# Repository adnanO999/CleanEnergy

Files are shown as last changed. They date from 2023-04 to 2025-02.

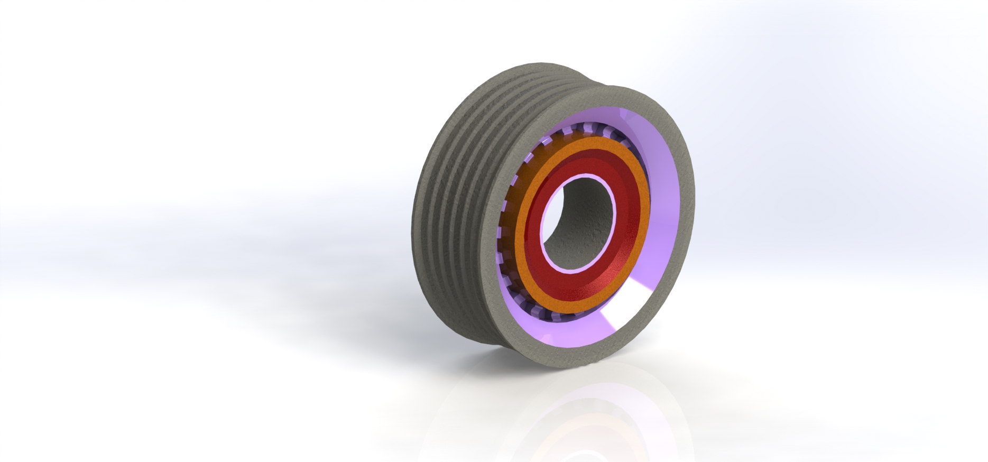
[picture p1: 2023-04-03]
SolarPanelCleaner/cad_parts/RoverCAD/pulley/PULLEY.JPG

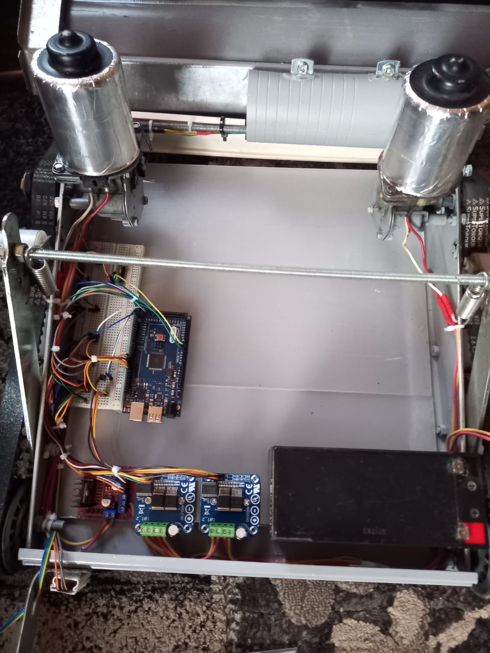
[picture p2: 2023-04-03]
SolarPanelCleaner/robot_pictures/wiring2 (2).jpeg

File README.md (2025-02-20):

# CleanEnergy
onsolarpanel

As it is obvious, the project is designed to clean solar panels. It might be an easy task however from simple observations, several problems might arise such as difficulties in covering the entire area, electrocution. Therefore I decided to build this project for the Mechatronics System design I. However I took one step further and used computer vision to detect the area of cleaning instead of relying only on sensors.

In this article I will be focusing on the implementation of each part and mainly the mechanical design wich was the core of the project and I was responsible of carrying out the design and implementation along with other tasks taht will be mentioned in what follows.

The project can be devided in several parts:
* Research 
* Mechanical design 
* assembling and wiring hardware 
* Code 
   * S shape path1 and path2 
   * Bluetooth communication/app 
   * MPU 6050 
* Report/presentaion
* Additional Improvements outside the course scope (personal work)

Each part will be expalined along

# Research and Motivation
## Dust and Efficiency Reduction


Solar energy is the most abundant of all energy resources and can be easily employed through the installation of solar panels constructed of photovoltaic cells (PV) that converts the sun radiation to electricity by a process of photon absorption and electrons excitation. 

However solar panels could experience efficiency reduction due to accumulated dust or unclean panels blocking solar radiation from interacting with PV cells. This is a major issue since the light obstruction materials (accumulation of dirt or particles like dust, sand, and moss) pose as external resistances that reduce solar photovoltaic performance. It was found that the external resistance could reduce the photovoltaic performance by up to 85% and the value of short circuit current, power decrease with respect the amount of dust on the solar panel.

## Modular Design and Angle Obstacle


we can notice that the first obstacle is the issue related to the angle. If we need to build a robot, we need to overcome slope slippage. This is a main challenge since our target is to build modular cleaning mechanism capable of covering different solar panels installation rather than static mechanism such as conventional wipers available for large firms

# Mechanical Design: Caterpillar Model

The previous issue of slopes cannot be resolved using a standard wheel-based robot since these types of robots have small wheels providing reduced contact area with the surface. Any plastic wheel will fail to provide the necessary grip to overcome slopes.
For this purpose I started my research and opted for caterpillar design. However the available robots in the market were very small or made of plastic which will not help.
For this reason I started several design iterations listed below with a brief description:

## Fisrt Design: Use of Car Seat and Customized Belts

As we can see the chassis is made of a car seat which was our initial starting point. We wanted to use the back of the seat as our cleaner since it had the ability to move up and down. Moreover we did not have appropriate belts thus we needed to cut one long belt and connect it. We discovered that the belts were not strongly bonded which will create slippage problems and malfunctioning when moving from one panel to the other

## Second Design: Customized Chassis Design and Use of car Window Motor

As we can notice this time, we designed a new compact chassis that include polyamide wheels that will help us moving from one panel to the other easily. Moreover, we can notice that we added a gear and motors to make the caterpillar move. However, the gears were customized to fit the belt teeth which led to slippage once some teeth were jumped over. To solve this problem, we needed to maintain good contact with our gear. This will be done using pulleys that compress the belt to the gear. 

## Third Design: New Belts and Use of Wiper Motor 

In this design we can see an enhancement of the previous design by adding fixed pulley to press the belt toward the gear. As such we avoid the case of belt’s teeth jumping more than one at a time. However, the problem is in the rigidity of the fixed pulley. When stress is coming from the bottom part, the belt will be in excessive tension around the gear which affects motion. To avoid this problem, we must use modular pulley to compress the belt toward the gear

## Fourth Design: Final Chassis Design 
### Tensioner Design: Unique Approach 


To move from fixed to modular pulley we were inspired by the car mechanism “tensioner.” We tried to implement a similar behavior by allowing pulley to move by spring mean. This design allows us to reduce tension on the gear when moving from panel to another and in case the panels are not aligned at the same height this will insure a perfect transition. 

 By following the distinctive design procedure, we successfully designed a differential rover capable of defeating and climbing slops. Our final chassis model is in the adjacent picture. As we can see the robot is standing on the panels without any problem.  
The effort put in the mechanical design is a considerable effort since it is not a conventional design available in the market. The rover is a customized and assembled part by part from different components that include customized belts, car pulleys used as wheels, polyamide wheels, and copper tubes fixing the wheels to the chassis, springs to support the moving pulley. We can say that as first step which is the base of the project is achieved by producing a successful model able to climb slopes. 

## Cleaning Mechanism: Gears and Chains to Convert and Translate Motion

The cleaning mechanism can be considered as our second challenge. The main difficulty consists in ensuring a brush able to clean the distance traveled by the robot. This can be done using two separate disks rotating each having a diameter equal to half the width of the robot. This is technically realizable however it implies the need of two motors each for one brush or the use of gear assembly like the differential gear where two brushes will be rotated by one motor. The second solution is to use one a single brush able to cover the width of the robot and a motor attached at one end. The problem faced in this approach was the motor installation which was solved by adding chain and gears between the motor and brush.

# Motor Selection
We applied the concepts learned throught the course, and detailed calculation was carried out to find a suitable motor. Ater all calculation we selected wiper motors.

# Wiring and Connections
All connections and wires were organized to have the best wiring schematic. Clean wiring to avoid connections issues. This is shown below:



# Algorithm
For the algorithm we used simple approach that relies on IR sensor to detect the presence of panel under the robot and using S shape algorithm we navigated along panels. Two issues arised:
## Chassis Drift: Motor Synchronization
Since we did not have encoders on our mototr we could not use encoder feedback to run the two motors at same speed therefore we relied on PWM signals and made the slowest motor's speed to be the mazimum speed. However a slight deviation remained, this problem will be solved as explained below:

## Which Direction to Rotate: Left or Right?
Since our design is modular and the user can put the robot on any corner, we need to be able to know our orientation. This problem is solved using MPU6050 where we read the angle to know if we are tilted left or right. To benefit more from the MPU6050 we used the acceleration and derived velocity combining with tilt angle to allow the robot to adjust its pose when deviating 

To test the accelerometer data, we coolected hundred of samples serialy through a python code which converts the reading to a csv file that can be ploted in matlab. We used matlab to analyze and process the data and the results obtained are shown below (we should mention that MPU6050 readings are noisy and drift with time therefore filters were used):




# Bluetooth Application
To give the user the ability to better ontrol the rover in case of any failure, We created a bluettoth application that helps navigating the robot. The application was built using MIT app and the hardware used was HC-05 bluetooth module:


# Further Work
## Computer Vision
This feature was under developement that allows the user to take a picture and send it to the rover allowing it to visualize and calculate the cleaning surface.
(the testing was done only on the PC since I did not establish a wireless connection between the rover and PC)
WhatsApp Image 2023-05-28 at 17 26 29

## Solidworks Model
I tried to design a solidworks model for further design enhancement



## Tracking the Rover
To obtain a closer look on how the robot is moving, I previously created a program that ensures communication between arduino, python and unity game engine.
The process works as follows: we need to add encoders to be able to get the better measurements for the displacement. Displacement and values accumulated MPU6050 can be combined and sent from aduino to python serialy (later we can use raspberrypi to eliminate the use of cable). The data collected in sent from python to unity and through a C# script I created a TCP or UDP connection based onpreference and the accuracy of data send and communication type. I followed an existing model to create this communication with a small modification in order to recieve the data in the correct format and shape.

# Summary
Solar panel cleaning rover This project aims to clean solar panels in more efficient and safe way. The design process followed several iterations and endedup using caterpillar model. The rover is designed to handle differnt slopes varying from 0 to 30 degree. A modular tensioner is mounted on both sides to enable smooth transition from on panel to the other and accomodate with height difference when moving across the panels. The Robot weight approximately 10 Kg however this weight can be reduced by removing the water tank and battery from the rover and mount them externally. S shape algorithm was used based on accelerometer and gyroscope data (pitch roll yaw angles) and projected on the panels surface. the microncontroller used was arduino mega thus processing was limited therefore I used serial communication to build python program to handle computer vision. Matlab and python codes were built using existing examples however with more modification to match our goal. These codes were used to collect data from accelerometer/gyroscope transform them to csv file and plot them to analyze the movement of the robot.

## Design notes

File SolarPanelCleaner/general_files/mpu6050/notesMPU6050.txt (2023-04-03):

1)IMU with 6 DOF. device contains gyroscope and accelerometer used to measure
inertia position rotation...

2)acceleration vs inertial force acting on the accelerometer (work in opposite direction)

3)guroscope used to measure angle orientation on three different levels(pitch rol yaw)
mems technology used in mpu6050. when an axis is rotated a voltage is produced.Voltage is sampled 
with 16 bits ADC inside the MPU6050

4)temperature sensor is implemented on the MPU6050 and DMP(digital motion process)
used to corrolate data from accelerometer and gyroscope

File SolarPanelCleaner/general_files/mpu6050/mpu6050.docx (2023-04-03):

1)IMU with 6 DOF (ability to move in three dimensions). device contains gyroscope and accelerometer used to measure

inertia position rotation...

2)acceleration vs inertial force acting on the accelerometer (work in opposite direction)

3)guroscope used to measure angle orientation on three different levels(pitch roll yaw)

mems technology used in mpu6050. when an axis is rotated a voltage is produced.Voltage is sampled

with 16 bits ADC inside the MPU6050

4)temperature sensor is implemented on the MPU6050 and DMP(digital motion process)

used to corrolate data from accelerometer and gyroscope

pin configuration

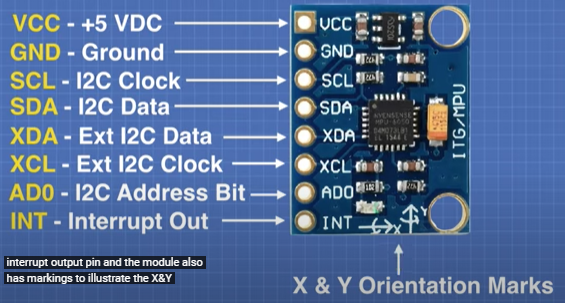
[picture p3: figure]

Info: https://www.dofbot.com/post/angle-measure-using-mpu-6050-3-axis-accelerometer-and-gyroscope-sensor

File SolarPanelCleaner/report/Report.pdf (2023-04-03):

# LEBANESE AMERICAN UNIVERSITY

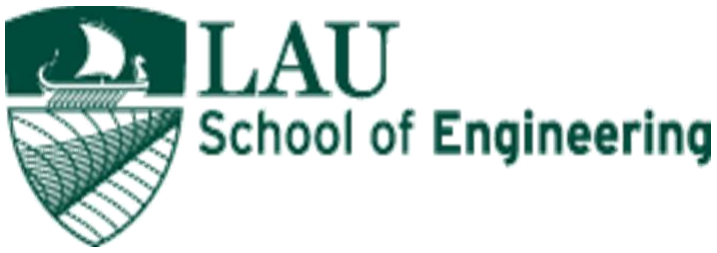
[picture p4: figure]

# Mechatronics System Design I Final Project

## Instructor: Dr Bilal Komati

## Dustbuddy: The Autonomous Solar Panel Cleaner

Table of Contents

Table of Figures
Figure 1 I-V characteristic and external resistance effects |
6
Figure 2 clean versus dusty solar panels |
7
Figure 5 first design (car seat chassis) |
10
Figure 9 Final chassis design defeating slopes (https://d.docs.live.net/2f20193610db98f5/Desktop/MCE_report%20edit.docx#_Toc122398008) . (https://d.docs.live.net/2f20193610db98f5/Desktop/MCE_report%20edit.docx#_Toc122398008) |
12 (https://d.docs.live.net/2f20193610db98f5/Desktop/MCE_report%20edit.docx#_Toc122398008)
Figure 10 Cleaning Mechanism (https://d.docs.live.net/2f20193610db98f5/Desktop/MCE_report%20edit.docx#_Toc122398009) . (https://d.docs.live.net/2f20193610db98f5/Desktop/MCE_report%20edit.docx#_Toc122398009) |
12 (https://d.docs.live.net/2f20193610db98f5/Desktop/MCE_report%20edit.docx#_Toc122398009)
Figure 11 Arduino Mega ADK |
13
Figure 13:BTS7960 (https://d.docs.live.net/2f20193610db98f5/Desktop/MCE_report%20edit.docx#_Toc122398012) . (https://d.docs.live.net/2f20193610db98f5/Desktop/MCE_report%20edit.docx#_Toc122398012) |
15 (https://d.docs.live.net/2f20193610db98f5/Desktop/MCE_report%20edit.docx#_Toc122398012)
Figure 14: L298N |
15
Figure 16: IR sensor module (https://d.docs.live.net/2f20193610db98f5/Desktop/MCE_report%20edit.docx#_Toc122398015) . (https://d.docs.live.net/2f20193610db98f5/Desktop/MCE_report%20edit.docx#_Toc122398015) |
16 (https://d.docs.live.net/2f20193610db98f5/Desktop/MCE_report%20edit.docx#_Toc122398015)
Figure 18: 9V battery (https://d.docs.live.net/2f20193610db98f5/Desktop/MCE_report%20edit.docx#_Toc122398017) . (https://d.docs.live.net/2f20193610db98f5/Desktop/MCE_report%20edit.docx#_Toc122398017) |
16 (https://d.docs.live.net/2f20193610db98f5/Desktop/MCE_report%20edit.docx#_Toc122398017)
Figure 19: connector cable (https://d.docs.live.net/2f20193610db98f5/Desktop/MCE_report%20edit.docx#_Toc122398018) . (https://d.docs.live.net/2f20193610db98f5/Desktop/MCE_report%20edit.docx#_Toc122398018) |
16 (https://d.docs.live.net/2f20193610db98f5/Desktop/MCE_report%20edit.docx#_Toc122398018)
Figure 20: 12V battery (https://d.docs.live.net/2f20193610db98f5/Desktop/MCE_report%20edit.docx#_Toc122398019) . (https://d.docs.live.net/2f20193610db98f5/Desktop/MCE_report%20edit.docx#_Toc122398019) |
16 (https://d.docs.live.net/2f20193610db98f5/Desktop/MCE_report%20edit.docx#_Toc122398019)
Figure 22: Bluetooth app screen (https://d.docs.live.net/2f20193610db98f5/Desktop/MCE_report%20edit.docx#_Toc122398021) . (https://d.docs.live.net/2f20193610db98f5/Desktop/MCE_report%20edit.docx#_Toc122398021) |
17 (https://d.docs.live.net/2f20193610db98f5/Desktop/MCE_report%20edit.docx#_Toc122398021)
Figure 23: Algorithm Flowchart |
18
Figure 24 initialization FSM |
18

Figure 25 paths FSM |
19
Figure 27: pump FSM |
20
Figure 29: Circuit Diagram |
21
Figure 30 accelerometer vs sample graph (https://d.docs.live.net/2f20193610db98f5/Desktop/MCE_report%20edit.docx#_Toc122398029) . (https://d.docs.live.net/2f20193610db98f5/Desktop/MCE_report%20edit.docx#_Toc122398029) |
23 (https://d.docs.live.net/2f20193610db98f5/Desktop/MCE_report%20edit.docx#_Toc122398029)
Figure 34: Linear acceleration VS sample graph (https://d.docs.live.net/2f20193610db98f5/Desktop/MCE_report%20edit.docx#_Toc122398033) . (https://d.docs.live.net/2f20193610db98f5/Desktop/MCE_report%20edit.docx#_Toc122398033) |
24 (https://d.docs.live.net/2f20193610db98f5/Desktop/MCE_report%20edit.docx#_Toc122398033)
Figure 35: Linear position VS sample graph (https://d.docs.live.net/2f20193610db98f5/Desktop/MCE_report%20edit.docx#_Toc122398034) . (https://d.docs.live.net/2f20193610db98f5/Desktop/MCE_report%20edit.docx#_Toc122398034) |
24 (https://d.docs.live.net/2f20193610db98f5/Desktop/MCE_report%20edit.docx#_Toc122398034)
Figure 36: Linear velocity VS sample graph (https://d.docs.live.net/2f20193610db98f5/Desktop/MCE_report%20edit.docx#_Toc122398035) . (https://d.docs.live.net/2f20193610db98f5/Desktop/MCE_report%20edit.docx#_Toc122398035) |
24 (https://d.docs.live.net/2f20193610db98f5/Desktop/MCE_report%20edit.docx#_Toc122398035)
Figure 37: tilt compensated accelerometer VS sample graph (https://d.docs.live.net/2f20193610db98f5/Desktop/MCE_report%20edit.docx#_Toc122398036) . (https://d.docs.live.net/2f20193610db98f5/Desktop/MCE_report%20edit.docx#_Toc122398036) |
25 (https://d.docs.live.net/2f20193610db98f5/Desktop/MCE_report%20edit.docx#_Toc122398036)

### Table of Tables

Table 1: Cost summary |
22

Introduction

Solar energy is the most abundant of all energy resources and can be easily employed through the installation of solar panels constructed of photovoltaic cells (PV) that converts the sun radiation to electricity by a process of photon absorption and electrons excitation. The development of industries and orientation toward green energy play a significant role in relying heavily on solar panels which lead eventually to reduce the emission of fuel and gas combustion.

For the mentioned reasons, people opt to install solar panels to procure their daily needs of electricity consumption. This is a fabulous alternative for avoiding skyrocketing electricity bills especially in Lebanon where also we have three hundred days of sunshine during the year.

However solar panels could experience efficiency reduction due to accumulated dust or unclean panels blocking solar radiation from interacting with PV cells. This is a major issue since the light obstruction materials (accumulation of dirt or particles like dust, sand, and moss) pose as external resistances that reduce solar photovoltaic performance. It was found that the external resistance could reduce the photovoltaic performance by up to 85% and the value of short circuit current, power decrease with respect the amount of dust on the solar panel.

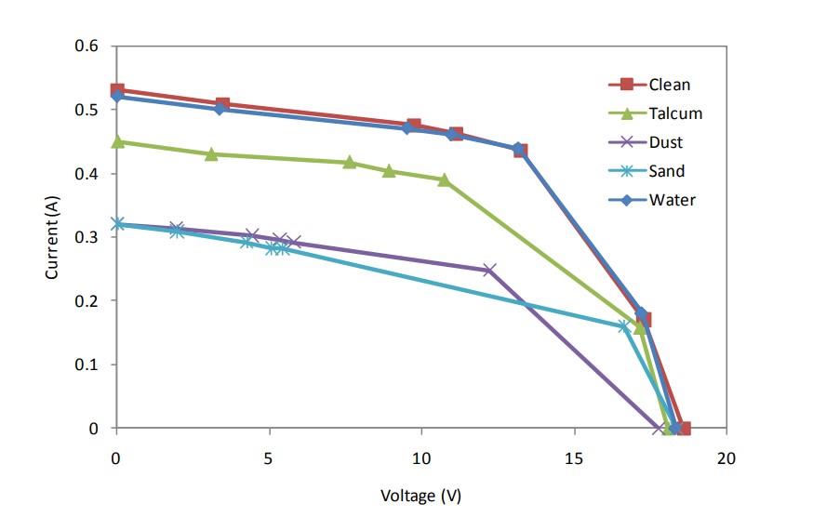
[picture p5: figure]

Figure 1 I-V characteristic and external resistance effects

Problem to Solve

From the above discussion we can say that natural dust is the one of the causes to reduce the output of the solar panel. To overcome these problems, a proper maintenance operation for the solar panels would be necessary. Particles like dust and sand can be reduced when washed away by water thus proper cleaning would be required. Therefore, to ensure cleaning maintenance we propose a solar panel cleaning robot that offers regular cleaning for the panels when needed. This could be useful also in saving lives. When it comes to solar panels, it is essential to be aware of the potential risks of cleaning them. Without proper safety precautions, a person can be electrocuted while cleaning photovoltaic cells. This is a severe hazard that you should not take lightly since you may not be grounded in the photovoltaic arrays.

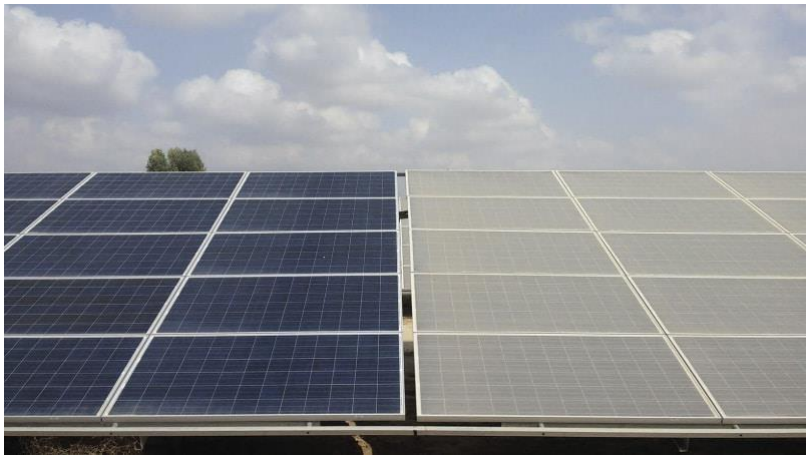
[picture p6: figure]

Figure 2 clean versus dusty solar panels

Project Specifications

It is evident that the installation of solar panels follows certain standards especially in large production firms. To collect solar power energy more efficiently, solar panels should be angled to face as close to the sun as possible. Photovoltaics produce power when the angle at which the sun‟s rays hit the panel surface (angle of incidence) is small, or when light strikes the panel as close to perpendicular as possible. Therefore, the best angle for your solar panels is the one that allows the panels to get the most direct, perpendicular light. For Lebanon, the solar panels should be installed at an angle around 25~35 degrees from the flat surface and should be facing south in an un-shaded area.

Figure 3 different angle orientation

From the above discussion we can notice that the first obstacle is the issue related to the angle. If we need to build a robot, we need to overcome slope slippage. This is a main challenge since our target is to build modular cleaning mechanism capable of covering different solar panels installation rather than static mechanism such as conventional wipers available for large firms.

The second challenge is to provide a suitable efficient cleaning mechanism that is capable of cleaning panels‟ surfaces rather than damaging them.

After making sure that we have a robot capable of withstanding slopes and providing efficient cleaning, we can move to the third challenge which is creating a cleaning algorithm.

Each task be solved alone, taking into consideration time and capacity constraints the project represents new moderated to hard challenges that require design, mechanical, and coding skills along with creative touch.

Design and Proposed Solutions

Chassis and Robot Structure
The first obstacle mentioned was the issue of slope climbing. This cannot be resolved using a standard wheel-based robot since these types of robots have small wheels providing reduced contact area with the surface. Any plastic wheel will fail to provide the necessary grip to overcome slopes. Additionally, when moving from panel to another they will fail due to the spacing between panels. Therefore, we can deduce that we need a non-wheel-based robot. We opted for a caterpillar design and started to search for available models. As first selection we chose the below model:

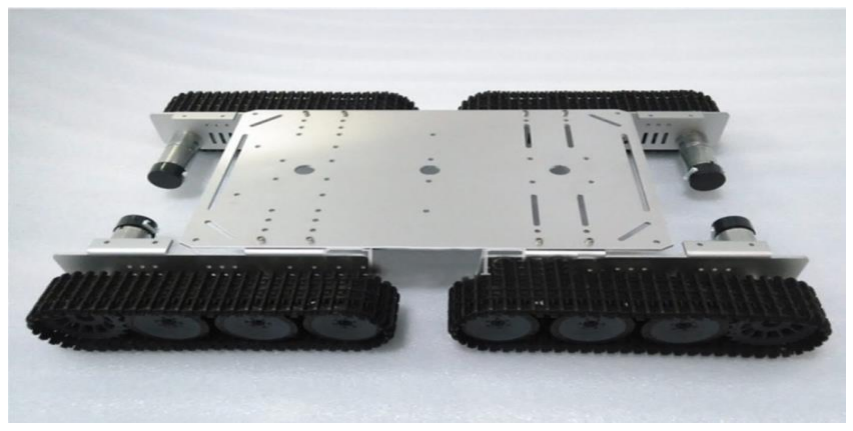
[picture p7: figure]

Figure 4 available caterpillar model

As first look one can see it as perfect design however the caterpillars were made of plastic along with a lightweight plastic and metal body and the dimension were small. As such the problem was intensified. All available models were overpriced and will lead eventually to failure. The only way to solve this problem is by creating our own design. Employing the idea of caterpillar, we built a customized powerful model defeating the conventional available models. We started with multiple design iterations and changed the structure based on the performance to finally meet the requirements. In What follows we will see the different model iterations:

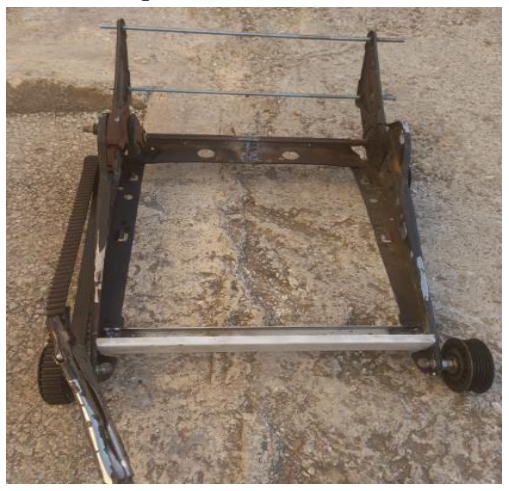
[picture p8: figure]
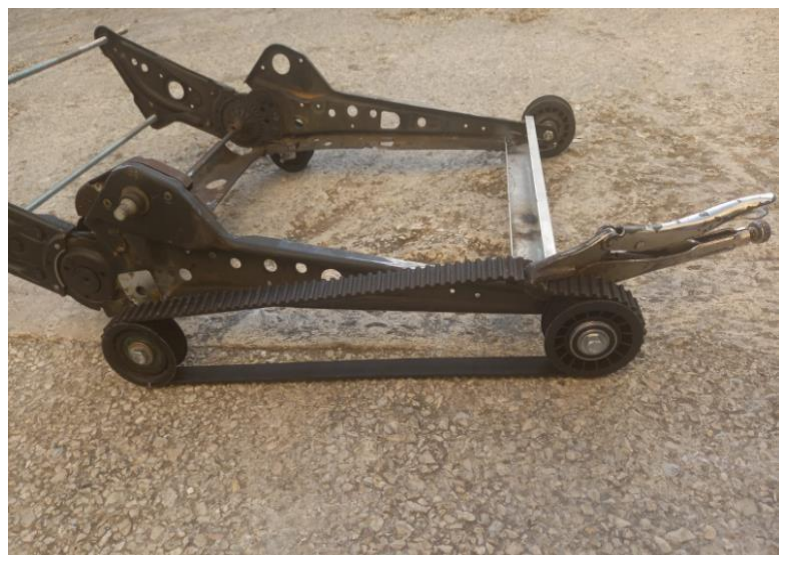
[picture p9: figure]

Figure 5 first design (car seat chassis)

As we can see the chassis is made of a car seat which was our initial starting point. We wanted to use the back of the seat as our cleaner since it had the ability to move up and down. Moreover, we did not have appropriate belts thus we needed to cut one long belt and connect it. We discovered that the belts were not strongly bonded which will create slippage problems and malfunctioning when moving from one panel to the other. The model was big which implies that we have a load problem. Thus, we reconsidered the design of the chassis.

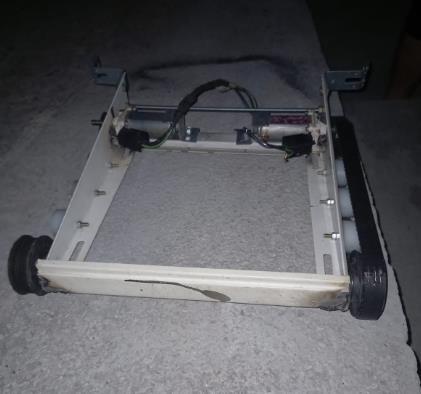
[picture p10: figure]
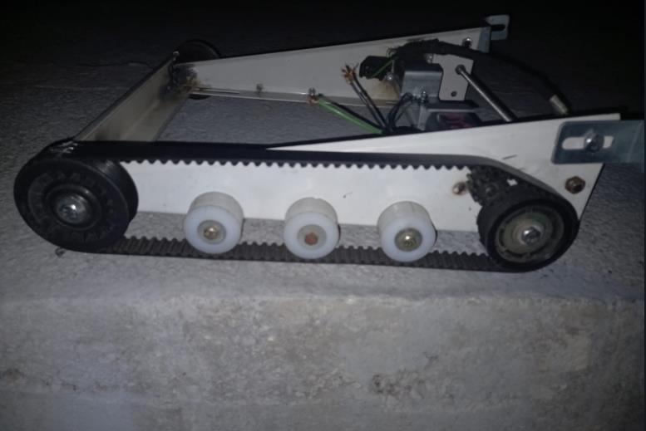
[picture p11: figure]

Figure 6 second design (enhanced chassis with polyamide wheels)

As we can notice this time, we designed a new compact chassis that include polyamide wheels that will help us moving from one panel to the other easily. Moreover, we can notice that we added a gear and motors to make the caterpillar move. However, the gears were customized to fit the belt teeth which led to slippage once some teeth were jumped over. To solve this problem, we needed to maintain good contact with our gear. This will be done using pulleys that compress the belt to the gear.

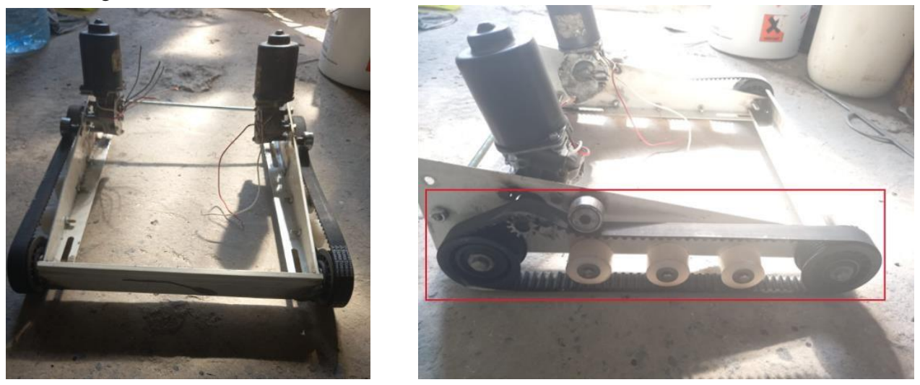
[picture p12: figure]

Figure 7 third design (with fixed belt pulleys)

In this design we can see an enhancement of the previous design by adding fixed pulley to press the belt toward the gear. As such we avoid the case of belt‟s teeth jumping more than one at a time. However, the problem is in the rigidity of the fixed pulley. When stress is coming from the bottom part, the belt will be in excessive tension around the gear which affects motion. To avoid this problem, we must use modular pulley to compress the belt toward the gear.

Figure 8 fourth design (modular pulleys with spring loaded “tensioner”)

To move from fixed to modular pulley we were inspired by the car mechanism “tensioner.” We tried to implement a similar behavior by allowing pulley to move by spring mean. This design allows us to reduce tension on the gear when moving from panel to another and in case the panels are not aligned at the same height this will insure a perfect transition.

By following the distinctive design procedure, we
successfully designed a differential rover capable of defeating and climbing slops. Our final chassis model is in the adjacent picture. As we can see the robot is standing on the panels without any problem.

The effort put in the mechanical design is a considerable effort since it is not a conventional design available in the market. The rover is a customized and assembled part by part from
different components that include customized
belts, car pulleys used as wheels, polyamide

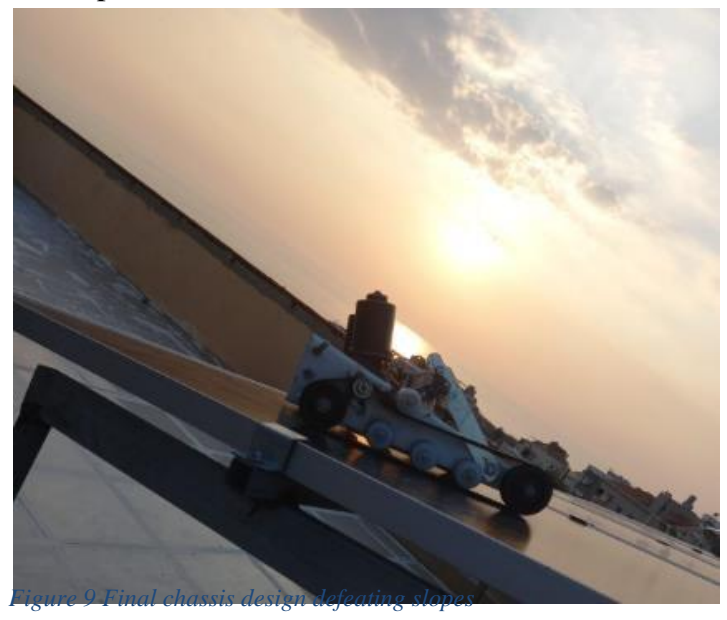
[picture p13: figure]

wheels, and copper tubes fixing the wheels to the chassis, springs to support the moving pulley. We can say that as first step which is the base of the project is achieved by producing a successful model able to climb slopes.

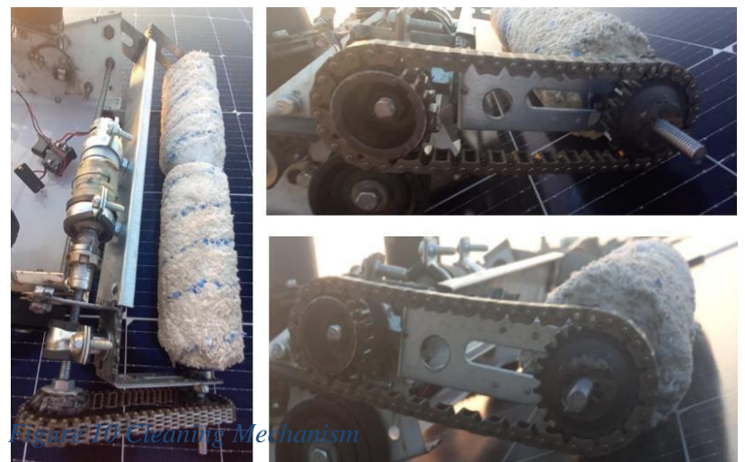
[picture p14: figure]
Figure 10 Cleaning Mechanism

Cleaning Structure

The cleaning mechanism can be considered as our second challenge. The main difficulty consists in

Figure 9 Final chassis design defeating slopes ensuring a brush able to clean the distance traveled by the robot. This can be done using two separate disks rotating each having a diameter equal to half the width of the robot. This is technically realizable however it implies the need of two motors each for one brush or the use of gear assembly like the differential gear where two brushes will be rotated by one motor. The second solution is to use one a single brush able to cover the width of the robot and a motor attached at one end. The problem faced in this approach was the motor installation which was solved by adding chain and gears between the motor and brush. The model is shown in the below picture:

Further explanation of the implemented functionalities and control mecanism will be provided in later sections in the report.
Hardware Used

In this section we will present the list of different hardware used along with the calculation needed to justify our choice.

Microcontroller
Every project contains a microcontroller responsible of executing programmable task. The selection of microcontroller is crucial since it will be the brain of the project delegating tasks and ensuring functionalities. In our case we chose the “Arduino Mega ADK” which is like the “Arduino Mega 2560” with one additional feature that it can be connected to android phones offering additional functionalities. This microcontroller was selected because we needed additional pins than those present in “Arduino UNO,” and it offers more memory and processing power.

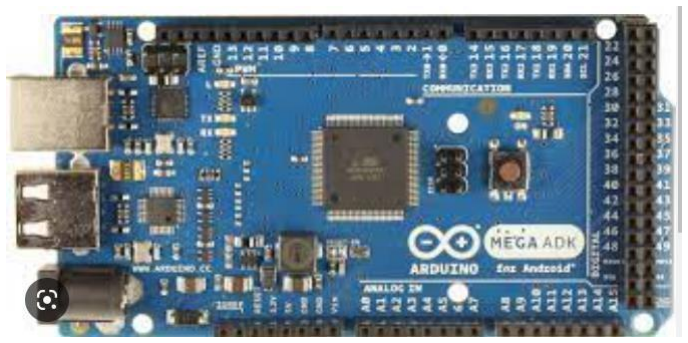
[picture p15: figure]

Figure 11 Arduino Mega ADK

Motor selection
The selection of our motors is a particularly major step in the design since we have slopes to climb along with the weight of the robot and other components such as power source water tank and electric components (we could design external power and water sources however we wanted these features to be embedded in the robot). As mentioned previously, our designed is based on differential meaning it is driven by two motors. The calculation done to approximate the size of needed motors is as follows:
- Step 1: determine the design constraints: speed, load, weight, climbing angle… o Weight of the robot: w = 10kg (including battery and water tank) o Maximum speed of the robot: v = 0.2m/s (belt speed driven by motor gear) o Maximum incline to climbs: θ = 40°
- Reach maximum speed in two seconds (acceleration) o Belt
length from center of the rear pulley to the front pulley:
- Step 2: Calculate the rotational speed of wheels:
(We can remove π since we are not converting to circumference and assuming the diameter of the pulley is added to the length of the belt since we are measuring from center to center)
- Number of turns: NT | 2L 0.46 | rpm
- Step 3: Calculate the motor force (thrust force) o If we omit friction, we can estimate the motor torque needed to climb the maximum slope previously specified. The force needed to overcome weight and gravitational acceleration can be calculated using Newton‟s second law
∑ F = ma o Assuming constant maximum speed of 0.2m/s and no initial speed we can calculate the acceleration using the equation of motion v − v0 = at. Solving for a: a = v = 0.1m/s
2
t o FT− mg ∗ sin(θ) = ma o FT= mg ∗ sin(θ) + ma o FT= 10 ∗ 9.81 ∗ sin(40)
+ 10 ∗ 0.1 ≈ x N
- Step 4: calculate power o Since the nominal speed is not specified, we will assume that the robot will be driven at constant maximum speed once starting to move. To calculate the power required: Pm = FT ∗ V = x ∗ 0.2 = y W
- Step 5: calculate torque o Mechanical power for the entire robot was found, so we
have y/2 W per one traction motor. The corresponding torque per motor: | ∗ R ∗
FT ≈ z Nm
- Step 6: summarize the values calculated o Rotational speed: NT = 27 rpm o Torque: TT = z Nm o Power:PT= y/2 W

Since we need a considerable torque, we need to consider using geared DC motors. After searching for available motor and comparing performance versus cost we selected motors used for car wipers. Below a brief description from datasheet:

TT =

1
2

As we can see, the wiper motors perfectly match our needed characteristics. The most important two features to extract from the provided description are operating voltage and current. We will operate the motor at 12 V where the current will vary ideally between 4.5 and 5 Ampere. For safety reasons we will consider the maximum output current to be 7~8 A.

Motor Driver Selection

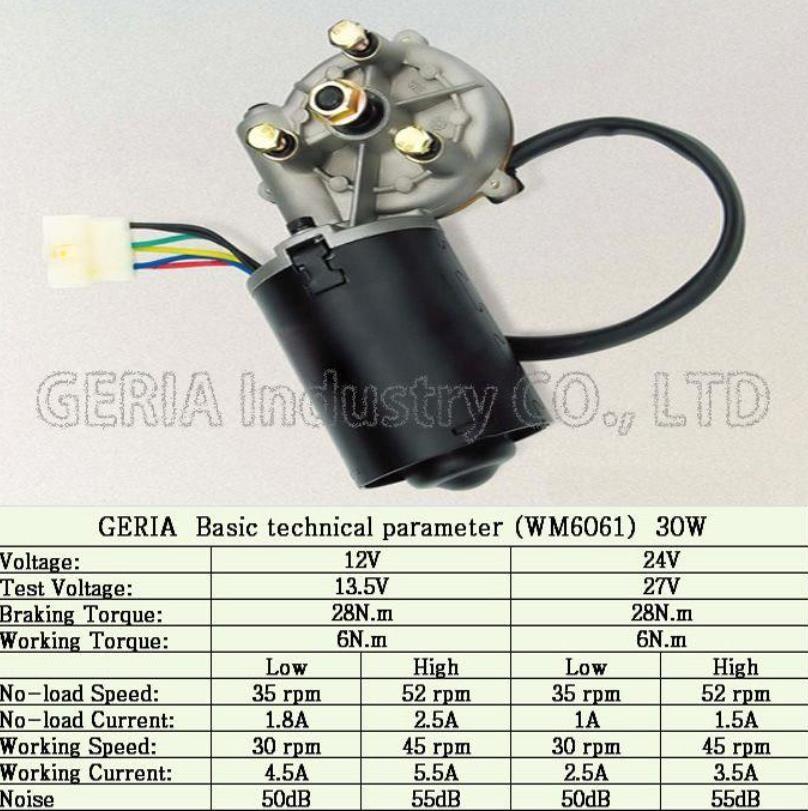
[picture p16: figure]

Figure 12 wiper motor specifications
After finding the max output current of the two motors we must find a suitable motor driver

The L298N motor driver has a maximum current of 4A which is less than our maximum current, so we cannot use this module.

We then researched to find 2 types of motor drivers DBH-01C Dual channel motor driver which has a maximum current of 20A which is suitable for our design however, it cost 35$ which is out of our price range, so we settled for two BTS7960 with a peak current of 43 Amps which cost 14$ each (28$ total).

We used the dual L298N motor driver for both the pump and the brush motor

Figure 13:BTS7960

Figure 14: L298N

Other Sensors
IR sensors
Our design uses 4 IR sensors (infrared sensors). An infrared sensor includes two parts namely the emitter & the receiver. The sensors send a digital either 0 or 1 to the Arduino. There are two sensors on each of the back and front side of the rover. These sensors are used to detect when the rover comes to the edge and determine how will the rover move based on the values of these IR sensors.

Accelerometer

Figure 16: IR sensor module
Our design uses the MPU6050 which consists of three axis accelerometer and three-axis

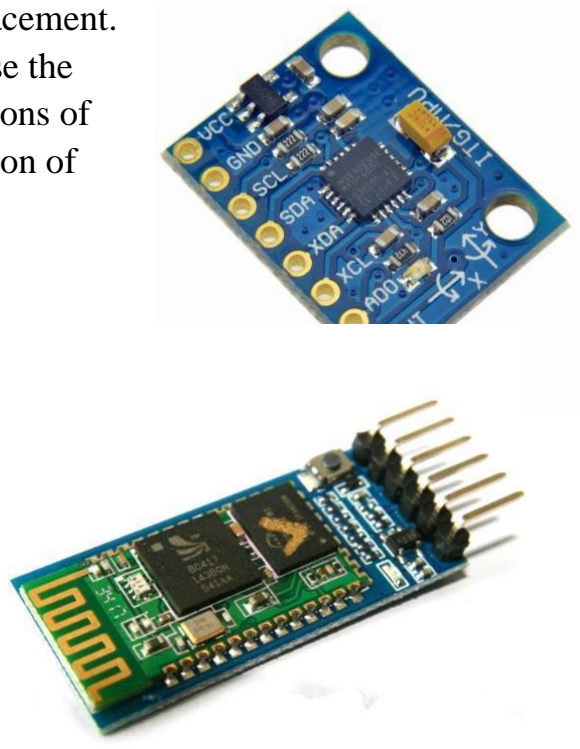
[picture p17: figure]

gyroscope. We can measure the velocity, orientation, acceleration, displacement.
To connect it to the Arduino we must install the MPU6050 libraries to use the features. The accelerometer was used to collect data of the X, Y, Z positions of
the rover and to determine the path of movement depending on the position of the rover in these planes.

Bluetooth Module
As an extra feature, we designed an android Bluetooth app to give access

Figure 15: MPU6050 to the user to navigate the rover and override the autonomous motion. This feature was attained by linking the Bluetooth app by the Arduino using HC05 Bluetooth module. The HC05 module is operated by connecting the Rx pin of the module to the Tx of the Arduino and the Tx pin to the Rx of the Arduino.

### Battery

To power the motors attached to the motor drivers a DC 12V battery with initial current 2.7A MAX.

To power the Arduino a 9V battery was used with its cable | Figure 17: HC05
Figure 20: 12V battery | Figure 18: 9V battery | Figure 19: connector cable

### Pump

To transfer water from the tank to the brush we used the R385 Mini
Aquarium Water Pump DC 6V- 12V

Figure 21: R385 water pump
Bluetooth Application
The Bluetooth application designed using MIT app inventor which contains:
- Devices to connect to the Bluetooth module (HC05)
- Four buttons to navigate robot (Forward, Backward, Turn Left, Turn Right)
- Pump button to flow water to the brush to clean
- A brush switch to turn the brush‟s motor on and off
- Two text boxes for the user to input the height and the width of the panel (this is used to store data)
- A stop button to stop the rover

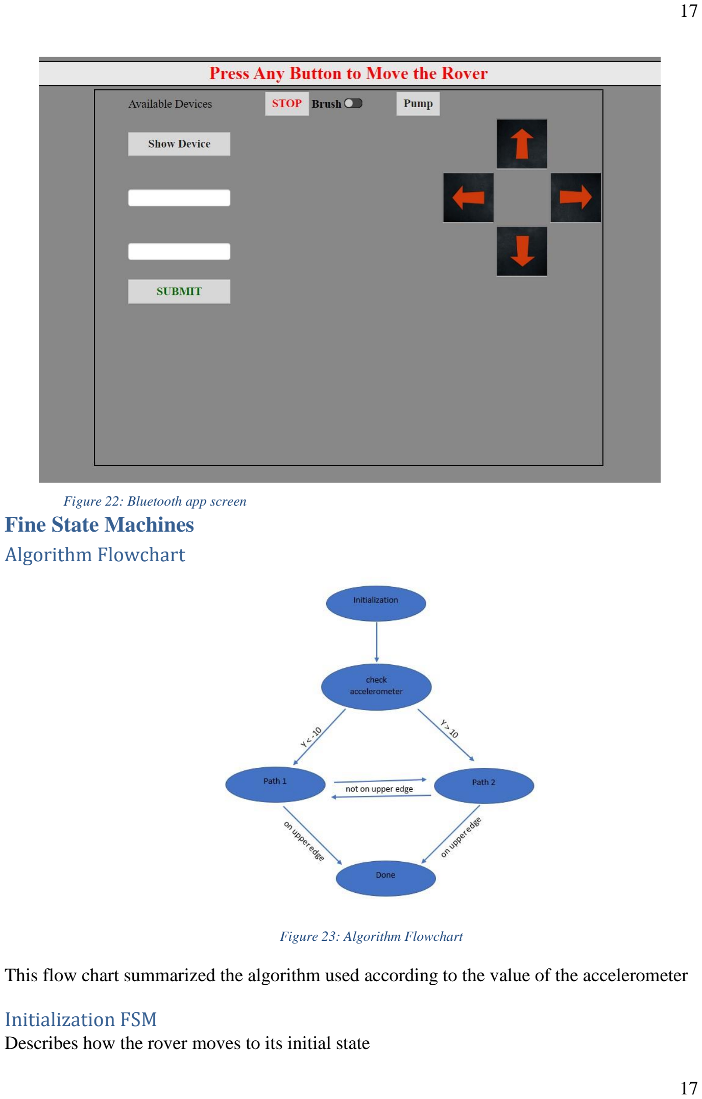
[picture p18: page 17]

Figure 22: Bluetooth app screen
Fine State Machines

### Algorithm Flowchart

Figure 23: Algorithm Flowchart

This flow chart summarized the algorithm used according to the value of the accelerometer

### Initialization FSM

Describes how the rover moves to its initial state

Figure 24 initialization FSM

### Paths FSM

Descries the trajectory of the rover depending on the IR sensors

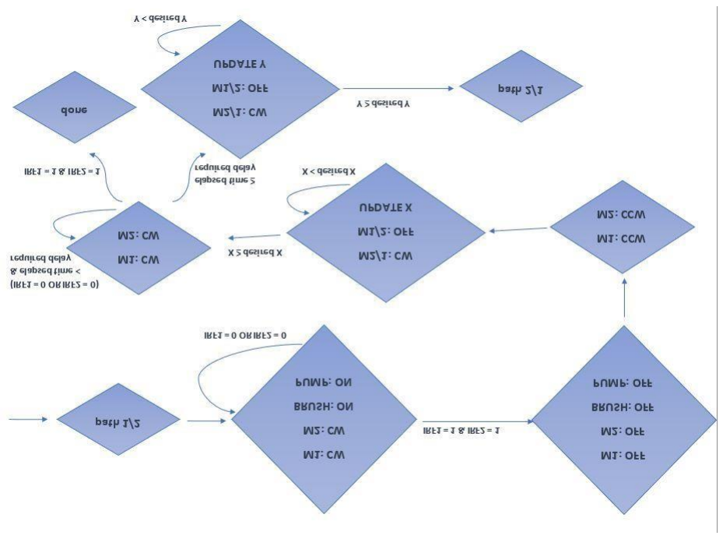
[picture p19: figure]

Figure 25 paths FSM

### Done FSM

Describes the path when the rover reaches the edge

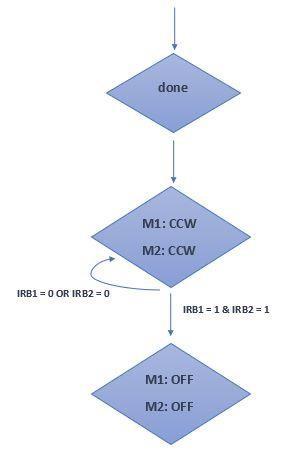
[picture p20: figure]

Figure 26 done FSM

### Pump FSM

Describes how the pump sprinkles water and stops on different time intervals

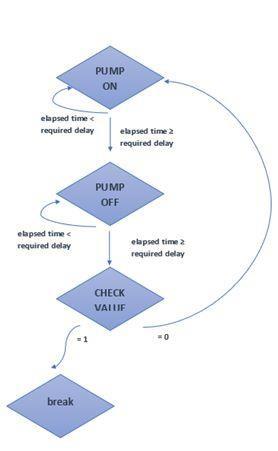
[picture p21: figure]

Figure 27: pump FSM

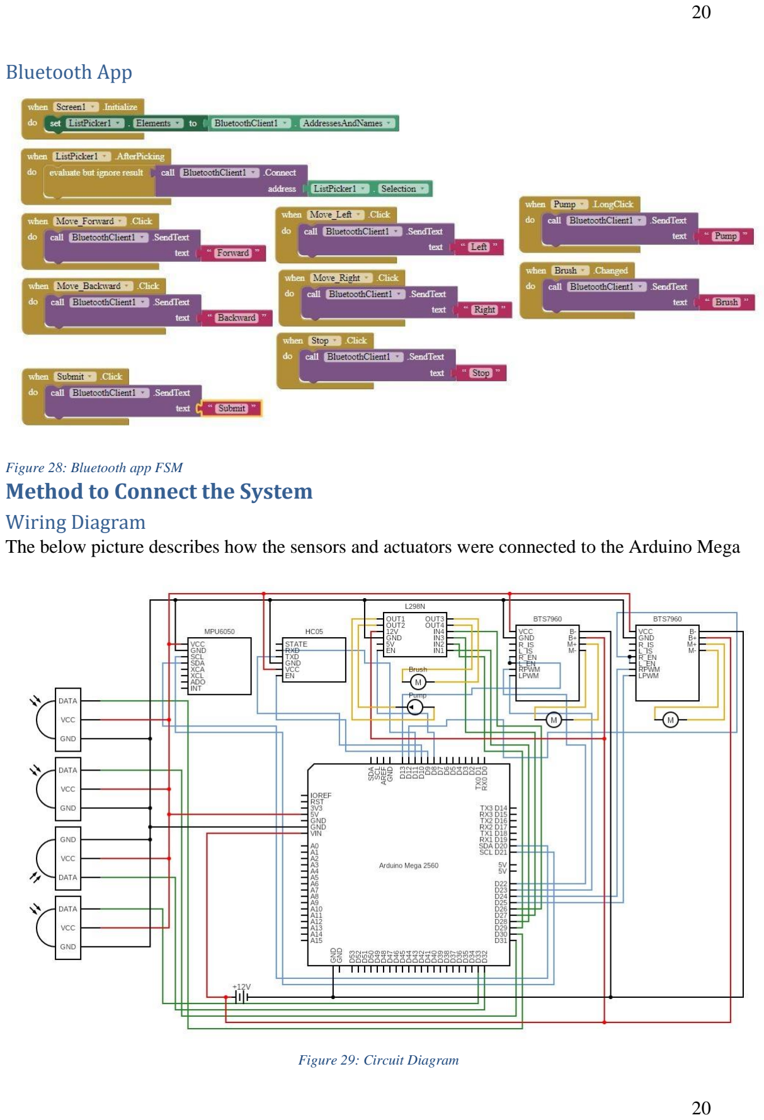
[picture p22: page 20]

### Bluetooth App

Figure 28: Bluetooth app FSM

### Method to Connect the System

### Wiring Diagram

The below picture describes how the sensors and actuators were connected to the Arduino Mega

Figure 29: Circuit Diagram

### Cost

Item | Price $ | Quantity | Total $
Arduino Mega | 38 | 1 | 38
Battery 12V | 8 | 1 | 8
Battery 9V | 2 | 1 | 2
Chassis | 65 | 1 | 65
Wiper Motor 1 | 17 | 2 | 34
Drill Motor 2 | 25 | 1 | 25
BTS7960 | 14 | 2 | 28
L298N | 3 | 1 | 3
HC04 | 5 | 1 | 5
MPU6050 | 4 | 1 | 4
Brush | 5 | 1 | 5
IR sensor | 1 | 4 | 4
Pump | 5 | 1 | 5
226

Table 1: Cost summary

Procedure Followed for Testing
First, after designing the chassis the model was tested against slippage and transition from panel to the other before proceeding with other tasks (Refer to figure 9). Then, we placed the chassis on a table to test the codes related to the IR sensors; if the IR detected „1‟ it will proceed with the following command (stop or turn back), else it will continue moving. We then tested the speed of the motors and tried to synchronize them to have the desired rotation. Next, we tested each method (Initiation, Path 1, Path 2) alone to simplify the debugging procedure. Then, the same methods were tested among the inclined plane to ensure that the rover does not slip and functions normally. Then, the brush and pump codes were tested and were functioning at the programmed time. After that, the Bluetooth application was tested to ensure proper functionality. Finally, we proceeded to join all pieces of code together to finalize the Arduino code and did all necessary final tests to finalize the project.

Results and Analysis
We collected almost one thousand samples from the MPU6050 the following results are described in the graphs below:

As shown aside the
accelerometer Vs sample graph (Figure 28) the Z component was ranging between 8g and 10g, X

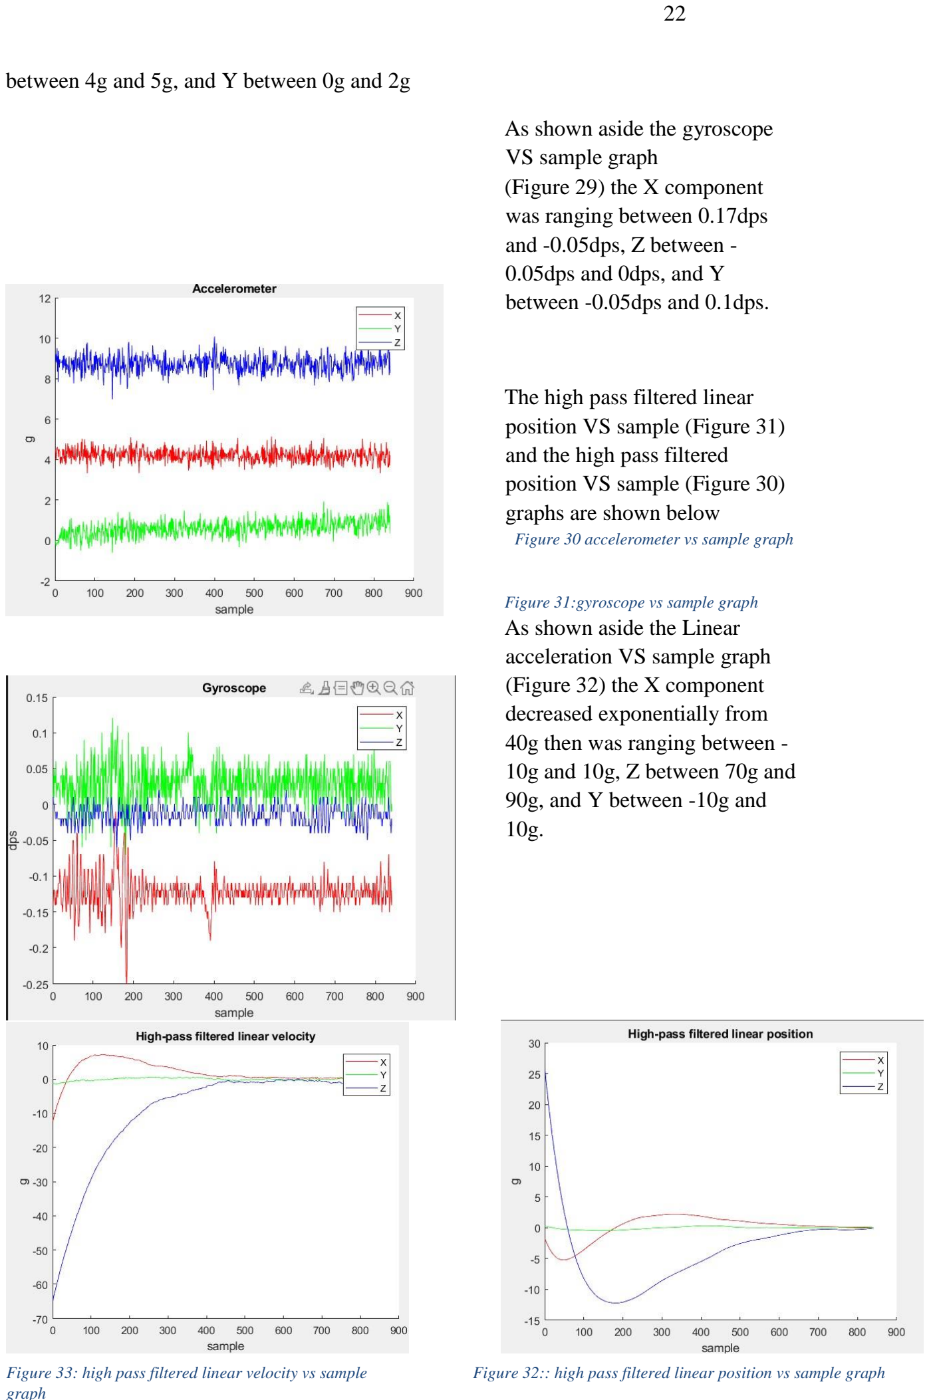
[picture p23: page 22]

between 4g and 5g, and Y between 0g and 2g

As shown aside the gyroscope VS sample graph
(Figure 29) the X component was ranging between 0.17dps and -0.05dps, Z between -
0.05dps and 0dps, and Y
between -0.05dps and 0.1dps.

The high pass filtered linear position VS sample (Figure 31) and the high pass filtered position VS sample (Figure 30) graphs are shown below

Figure 30 accelerometer vs sample graph

Figure 31:gyroscope vs sample graph
As shown aside the Linear
acceleration VS sample graph (Figure 32) the X component decreased exponentially from 40g then was ranging between -10g and 10g, Z between 70g and 90g, and Y between -10g and 10g.
Figure 33: high pass filtered linear velocity vs sample | Figure 32:: high pass filtered linear position vs sample graph
graph

As shown aside the Linear position VS sample graph (Figure 33) the X component decreased a bit and then increased to remain constant at 20g, Z decreased from 0g -100g and remained constant at that value, and Y remained constant at 0g.

As shown aside the Linear velocity VS sample

graph (Figure 34) the X
component increased to a
constant value of 50g, Z
increased linearly from 0g to 1000g, and Y remained
constant at 0g.

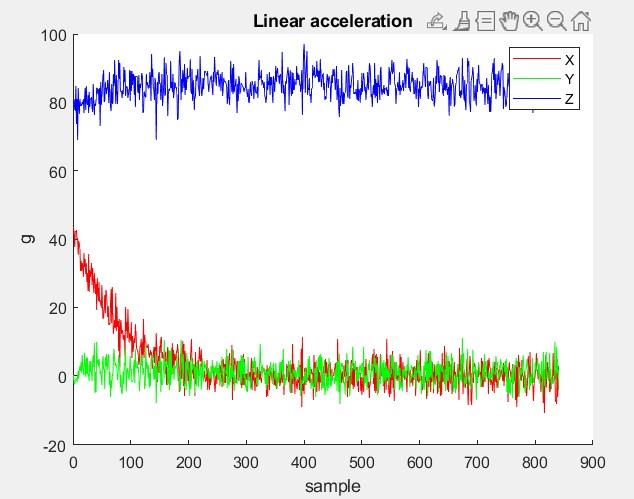
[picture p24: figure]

Figure 34: Linear acceleration VS sample graph

Figure 35: Linear position VS sample graph

Figure 36: Linear velocity VS sample graph

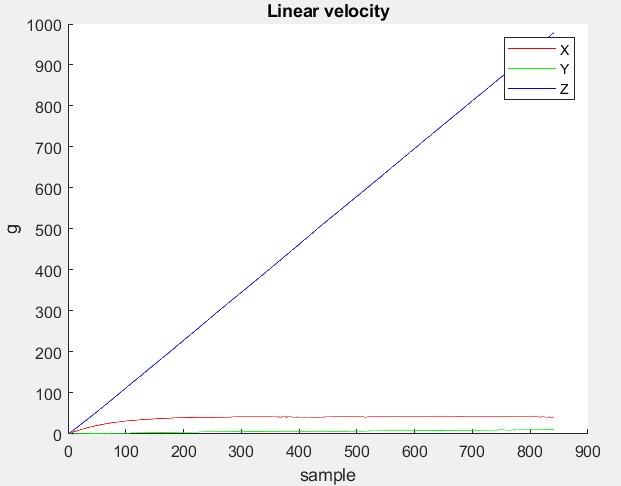
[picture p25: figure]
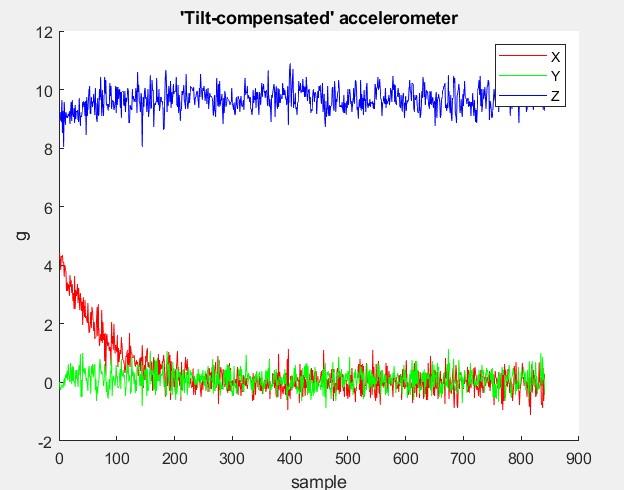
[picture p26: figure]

As shown aside the tilt compensated accelerometer VS sample graph (Figure 35) the X component decreased exponentially from 4g then was ranging between 0g and 1g, Z between 8g and 11g, and Y between -1g and 1g. (like the Linear acceleration VS sample graph (Figure 32)

Figure 37: tilt compensated accelerometer VS sample graph

The unfiltered XYZ curve shows the position calibration by offsets as X, Y, Z components and as U, V, W vectors as shown on the curve (figure 36)


Figure 38: unfiltered XYZ curve

Possible Amelioration
Possible Amelioration for the future could be:
- Reduction in rover‟s mass; the rover is almost 15kg and is heavy for the user to lift considering the transfer from the ground to the solar panel. Such improvement could occur by using a lightweight battery and drone like material (light in weight), but such improvements are a bit expensive.
- Making the wheels faster; to stop slippage, the rover was moving along a certain speed, thus, to finish cleaning the panels, it will take enough time to clean.
- Adding sensors to the tank to indicate when it is empty, such feature will have to override the rover‟s motion to stop the action and return to the initial position for the user to fill, but it requires a GPS to return to the position it was and continue from where it was stopped.
- Using a camera to enhance cleaning. Consider a spot which was not cleaned by the rover by just passing above it once, a camera enables the rover to make sure the panel is clean and will clean the dirty spots left.

- Adding grip so that the rover can navigate along inclined planes with a higher angle without slipping.

### References

Circuit Diagram - A Circuit Diagram Maker (circuit-diagram.org)

MIT App Inventor (http://ai2.appinventor.mit.edu/#6090263333044224)

ElectroSLab (https://electroslab.com/) – (https://electroslab.com/) Electroslab (https://electroslab.com/)

Home | Electronics Katrangi Trading (katranji.com)

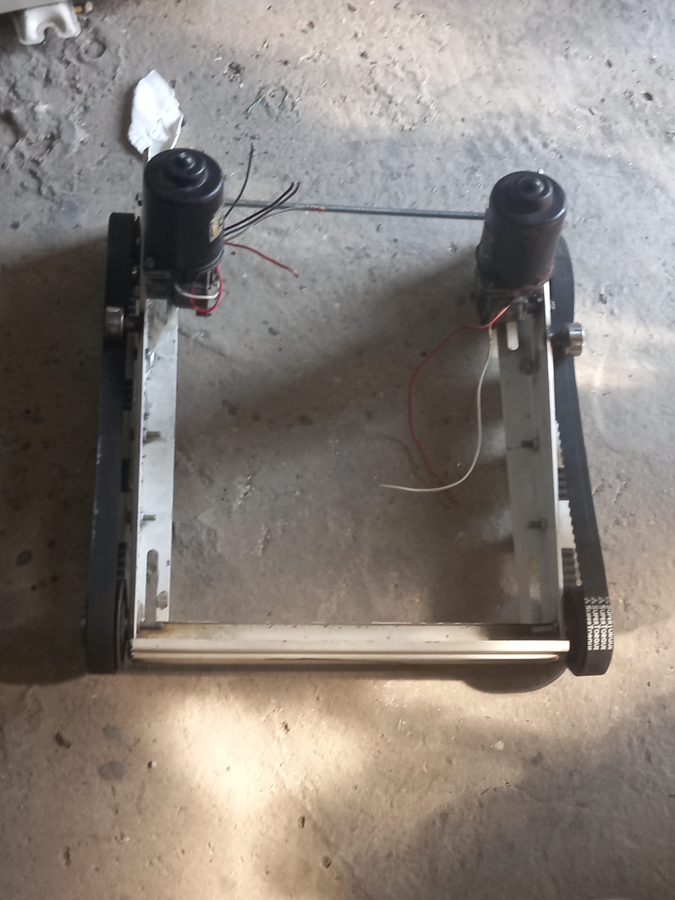
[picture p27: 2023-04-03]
SolarPanelCleaner/robot_pictures/topview_design2 (2).jpeg

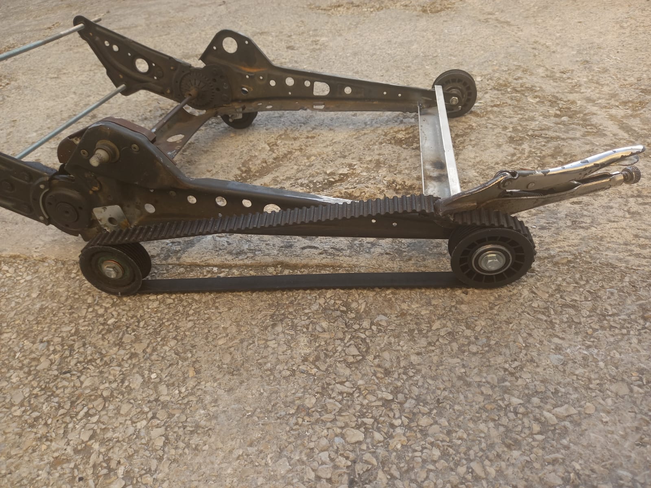
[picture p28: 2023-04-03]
SolarPanelCleaner/robot_pictures/design1.1 (2).jpeg

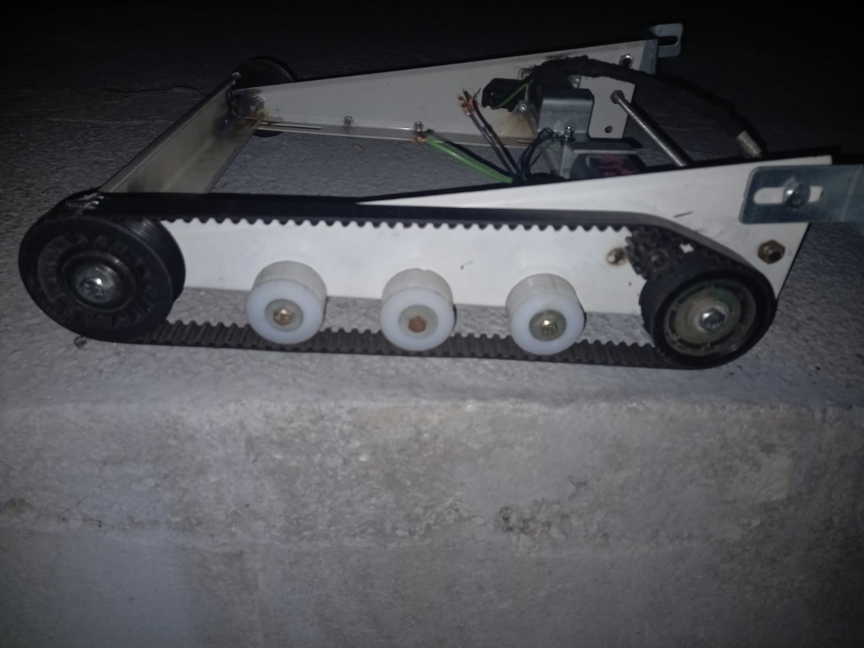
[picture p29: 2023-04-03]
SolarPanelCleaner/robot_pictures/design1.2 (2).jpeg

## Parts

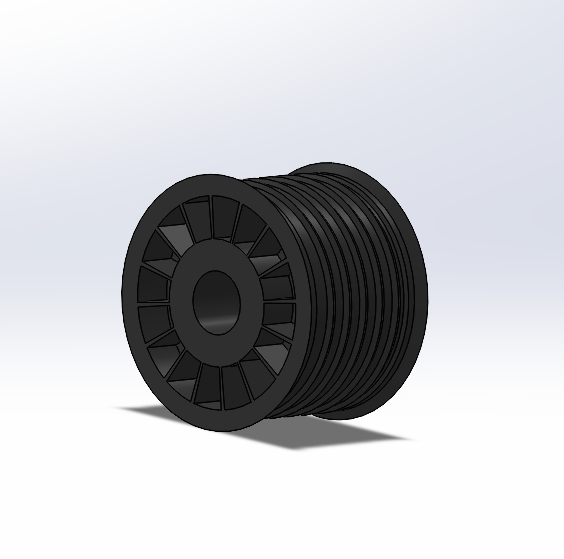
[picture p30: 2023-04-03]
SolarPanelCleaner/cad_parts/RoverCAD/pulley_wheel.png

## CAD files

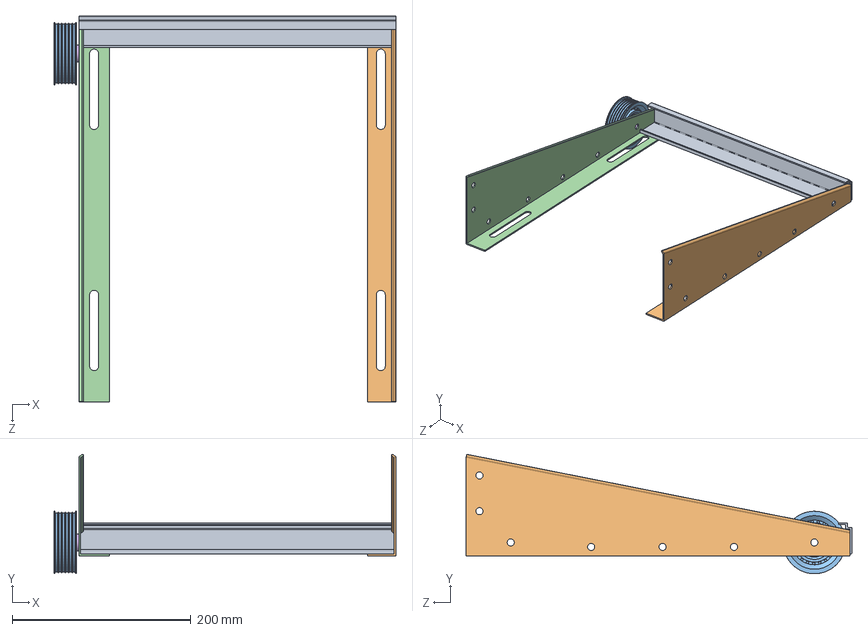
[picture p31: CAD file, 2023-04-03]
SolarPanelCleaner/cad_parts/RoverCAD/Assem1.SLDASM
382.9 x 133.7 x 432.0 mm
Link
SupportRight
Pulley
SupportLeft
pulleyBearing
pulleyExtender

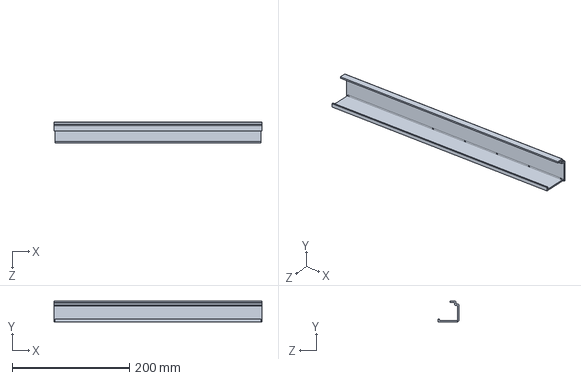
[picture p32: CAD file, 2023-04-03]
SolarPanelCleaner/cad_parts/RoverCAD/myrover/Link.SLDPRT
355.0 x 35.0 x 35.0 mm

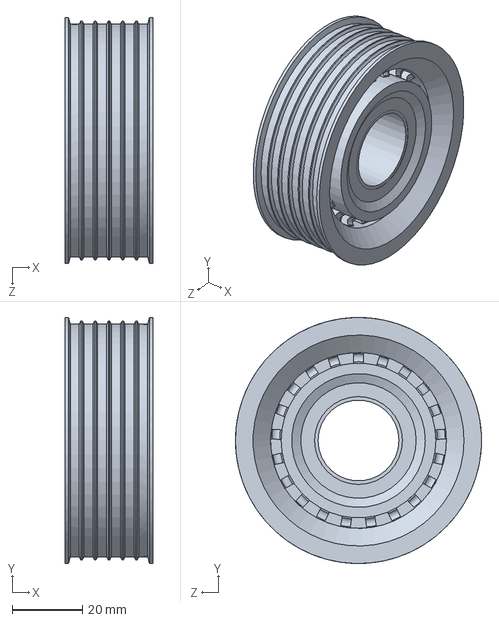
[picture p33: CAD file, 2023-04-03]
SolarPanelCleaner/cad_parts/RoverCAD/pulley/Pulley.SLDPRT
25.0 x 70.0 x 70.0 mm

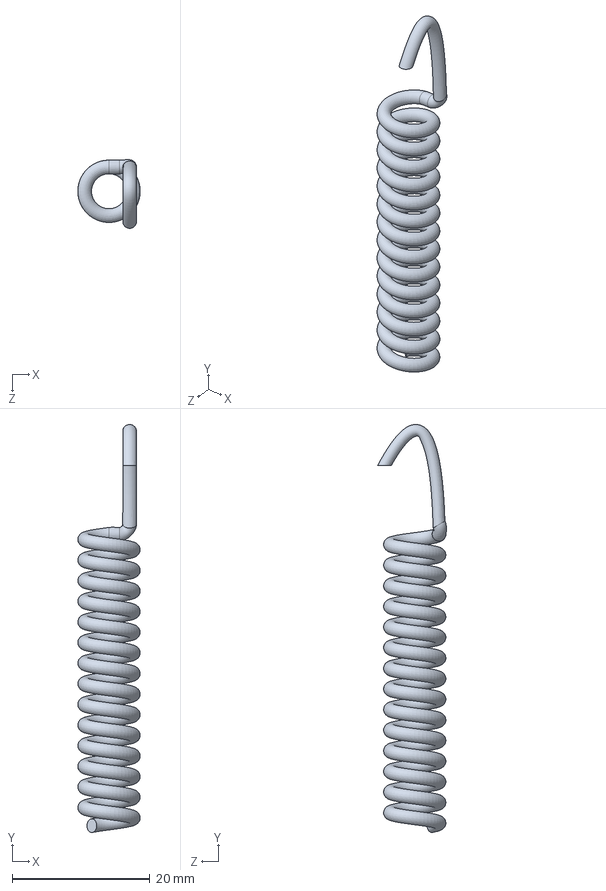
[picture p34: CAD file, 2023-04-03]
SolarPanelCleaner/cad_parts/RoverCAD/spring/Spring.SLDPRT
9.07 x 59.3 x 10.0 mm

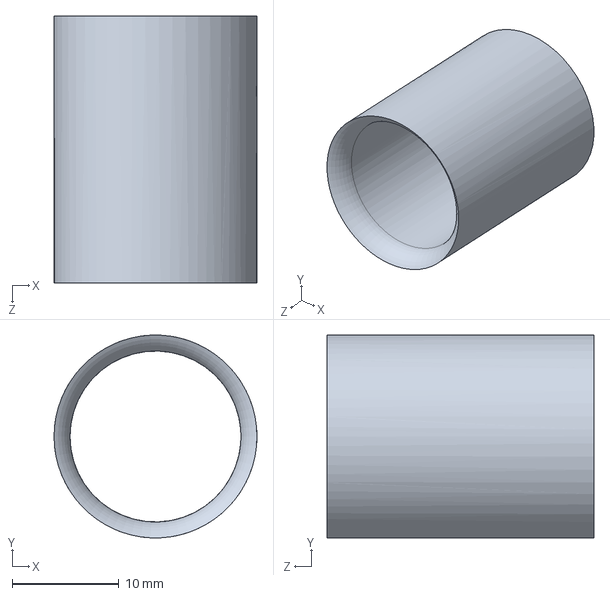
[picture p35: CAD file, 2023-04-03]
SolarPanelCleaner/cad_parts/RoverCAD/myrover/pulleyExtender.SLDPRT
19.0 x 19.0 x 25.0 mm

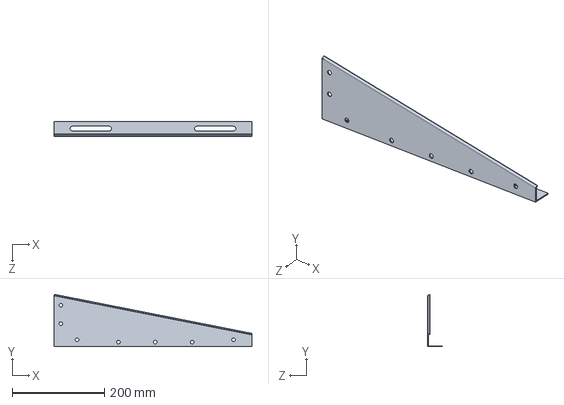
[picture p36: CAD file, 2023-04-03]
SolarPanelCleaner/cad_parts/RoverCAD/myrover/SupportRight.SLDPRT
430.0 x 113.7 x 32.0 mm

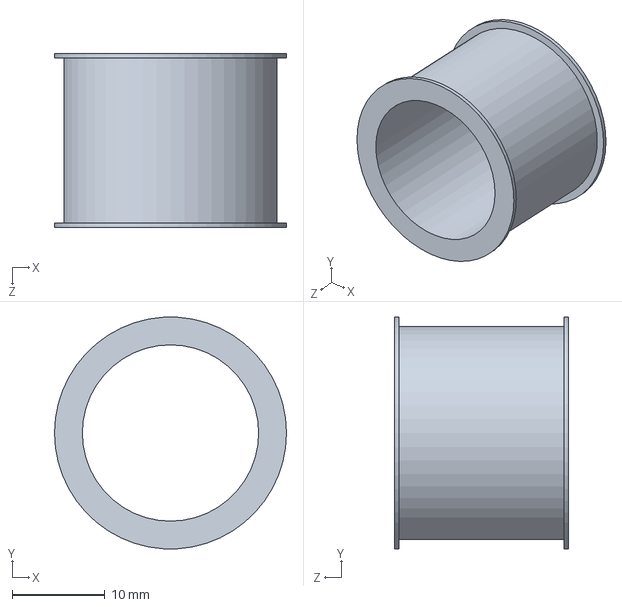
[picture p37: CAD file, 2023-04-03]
SolarPanelCleaner/cad_parts/RoverCAD/myrover/pulleyBearing.SLDPRT
25.0 x 25.0 x 18.8 mm

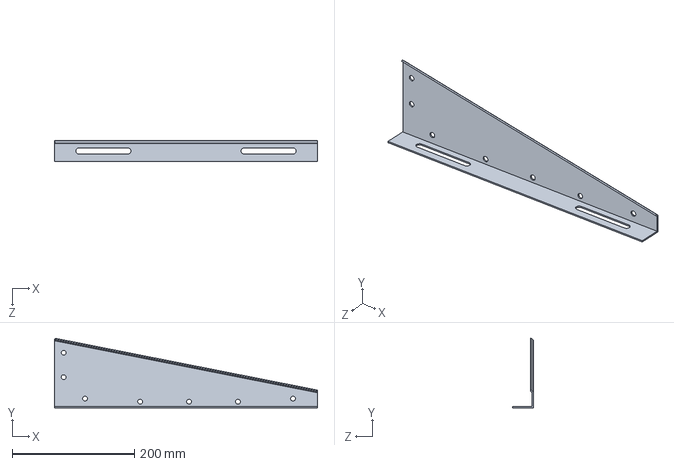
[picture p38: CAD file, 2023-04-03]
SolarPanelCleaner/cad_parts/RoverCAD/myrover/SupportLeft.SLDPRT
430.0 x 113.7 x 34.0 mm

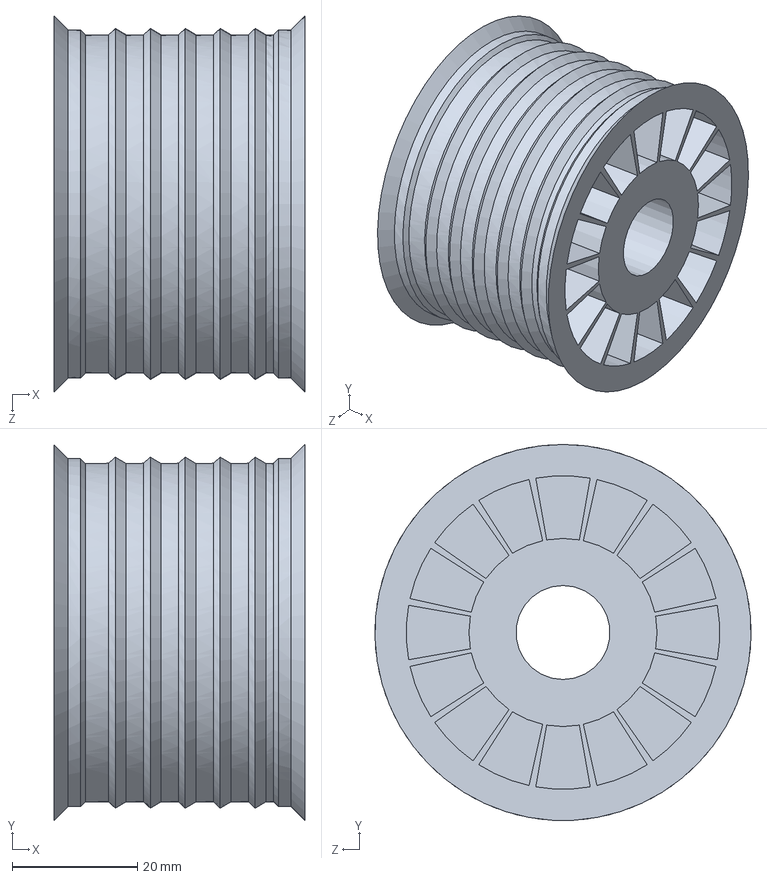
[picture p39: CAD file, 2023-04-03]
SolarPanelCleaner/cad_parts/RoverCAD/myrover/pulley.SLDPRT
40.0 x 60.0 x 60.0 mm

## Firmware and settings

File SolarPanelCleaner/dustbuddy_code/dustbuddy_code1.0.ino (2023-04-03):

#include <SoftwareSerial.h>
#include <Wire.h>


#include <Adafruit_MPU6050.h>
#include <Adafruit_Sensor.h>
#include <MPU6050_light.h>

MPU6050 mpu(Wire);
float x_angle = 0;
float y_angle = 0;
float z_angle = 0;

#define IRF1 33
#define IRF2 32
#define IRB1 31
#define IRB2 30

#define Pin_D1_L1  22
#define Pin_D2_L1  23
#define Pin_E_L1   9
#define Pin_D1_L2  24
#define Pin_D2_L2  25
#define Pin_E_L2   8

int count = 0;
int pump = 0;
int statePump = 0;
unsigned long prevTime = 0;
const long  delayON = 3000;
const long  delayOFF = 4000;

#define brushPin1 27
#define brushPin2 26
#define brushPWM 6

#define pumpPin1 27
#define pumpPin2 26
#define pumpPWM 6

# define TxD 11
# define RxD 10
SoftwareSerial BlueTooth (TxD,RxD);
char BT_input;

float Xval = 0;
float Yval1 = 0;
float Yval2 = 0;

void setup() {
  ////////////ACCELEROMETER GYROSCOPE//////////////
  Serial.begin(115200);
  while (!Serial)
    delay(10); // 

  Serial.println("Adafruit MPU6050 test!");

  // Try to initialize!
  if (!mpu.begin()) {
    Serial.println("Failed to find MPU6050 chip");
    while (1) {
      delay(10);
    }
  }
  Serial.println("MPU6050 Found!");

  
  
  delay(100);

//////////////////////////////////////////////////////////

  BlueTooth.begin(115200);  
  Serial.begin(115200);
  
  pinMode (IRF1, INPUT);
  pinMode (IRF2, INPUT);
  pinMode (IRB1, INPUT);
  pinMode (IRB2, INPUT);
  pinMode (Pin_D1_L1, OUTPUT);
  pinMode (Pin_D2_L1, OUTPUT);
  pinMode (Pin_E_L1, OUTPUT);
  pinMode (Pin_D1_L2, OUTPUT);
  pinMode (Pin_D2_L2, OUTPUT);
  pinMode (Pin_E_L2, OUTPUT);
  motor_stop1();
  motor_stop2();

  
  Serial.begin(9600);  
  Wire.begin();
  mpu.begin();
  mpu.calcGyroOffsets();

  initialize();

}

void loop() {
if (Serial.available())
  {
    String  Command = Serial.readString();
    if (Command == "Forward")
    {
      //Move Forward
      motor_CW1();
      motor_CW2();
    }
    else if (Command == "Backward")
    {
      //Move backward
     motor_CCW1()
     motor_CCW2()
    }
    else if (Command == "Left")
    {
      motor_CW1();
      motor_CCW2()
    }
    else if (Command == "Right")
    {
      motor_CCW1()
      motor_CW2();
    }
    
    if (Command == "Pump")
    {
      motorPump_ON();
    }
    if (Command == "Brush")
    {
      if (brushPin1 == HIGH){
        digitalWrite(brushPin1, LOW);
      }
      else if (brushPin1 == LOW){
        digitalWrite(brushPin1, HIGH);
        analogWrite(brushPWM, 250);
      }
    }
    if (Command = "Stop"){
        motor_stop1();
        motor_stop2();
    }
  }
}
}

void initialize(){
  Serial.begin(9600);
  int SF1 = digitalRead (IRF1);
  int SF2 = digitalRead (IRF2);
  int SB1 = digitalRead (IRB1);
  int SB2 = digitalRead (IRB2);

  motor_CCW1();
  motor_CCW2();
  while(SB1 == 0 || SB2 == 0){
     SB1 = digitalRead (IRB1);
     SB2 = digitalRead (IRB2);
     Serial.println (SB1);
     Serial.println (SB2);
    delay(500);
  }
  
  Serial.println (SB1);
  Serial.println (SB2);
  motor_stop1();
  motor_stop2();
  delay(1000);
  motor_CW1();
  motor_CW2();
  delay(1200);
  motor_stop1();
  motor_stop2();

  Serial.begin(9600);  
  Wire.begin();
  mpu.begin();
  mpu.calcGyroOffsets();


  float y = YaccValue();
  Xval = XaccValue()+ 90;


  if( y > 10){
    Yval1 = y;
    Yval2 = 0-y;
    path1();
  }else {
    Yval2 = y;
    Yval1 = 0-y;
    path2();
  }
  
}


void path1(){

  int SF1 = digitalRead (IRF1);
  int SF2 = digitalRead (IRF2);

  SF1 = digitalRead (IRF1);
  SF2 = digitalRead (IRF2);
  motor_CW1();
  motor_CW2();
  motorBrush_ON();
  pump = 1;
  pumpWater();

  
  while(SF1 == 0 || SF2 == 0 ){
   SF1 = digitalRead (IRF1);
   SF2 = digitalRead (IRF2);  
   delay(150);
  }

  pump = 0;

  motor_stop1();
  motor_stop2();
  motorBrush_OFF();
  delay(800);
  motor_CCW1();
  motor_CCW2();
  delay(6000);
  motor_stop1();
  motor_stop2();
  delay(800);
  float x = XaccValue();
  motor_CW2();
  while(x < Xval){
    x = XaccValue();
    delay(7); 
  }
  motor_stop2();
  motor_stop1();
  delay(800);

  motor_CW1();
  motor_CW2();

  SF1 = digitalRead (IRF1);
  SF2 = digitalRead (IRF2);
  count = 0;
  
  while( (SF1 == 0 || SF2 == 0)  && count < 10){
 
   SF1 = digitalRead (IRF1);
   SF2 = digitalRead (IRF2); 
   count += 1;  
   delay(150);
  
  }  
  
  motor_stop1();
  motor_stop2();
  
 if(SF1 == 1 && SF2 == 1){
    done();
  }else{
    motor_CCW1();
    motor_CCW2();
    delay(1500);
    motor_stop1();
    motor_stop2();
    delay(600);

    float y = YaccValue();
    motor_CW2();
    while (y > Yval2){
      y = YaccValue();
      delay(7);
    }
    
    motor_stop2();
    delay(600);
    motor_CCW1();
    motor_CCW2();
    delay(3000);
    motor_stop1();
    motor_stop2();
    
    path2();
  }

 
}


void path2(){

  int SF1 = digitalRead (IRF1);
  int SF2 = digitalRead (IRF2);

  SF1 = digitalRead (IRF1);
  SF2 = digitalRead (IRF2);
  motor_CW1();
  motor_CW2();
  motorBrush_ON();
  pump = 1;
  pumpWater();

  
  while(SF1 == 0 || SF2 == 0 ){
   SF1 = digitalRead (IRF1);
   SF2 = digitalRead (IRF2);  
   delay(150);
  }

  pump = 0;

  motor_stop1();
  motor_stop2();
  motorBrush_OFF();
  delay(800);
  motor_CCW1();
  motor_CCW2();
  delay(6000);
  motor_stop1();
  motor_stop2();
  delay(800);
  float x = XaccValue();
  motor_CW1();
  while(x < Xval){
    x = XaccValue();
    delay(7); 
  }
  motor_stop2();
  motor_stop1();
  delay(800);

  motor_CW1();
  motor_CW2();

  SF1 = digitalRead (IRF1);
  SF2 = digitalRead (IRF2);
  count = 0;
  
  while( (SF1 == 0 || SF2 == 0)  && count < 10){
 
   SF1 = digitalRead (IRF1);
   SF2 = digitalRead (IRF2); 
   count += 1;  
   delay(150);
  
  }  
  
  motor_stop1();
  motor_stop2();
  
 if(SF1 == 1 && SF2 == 1){
    done();
  }else{
    motor_CCW1();
    motor_CCW2();
    delay(1500);
    motor_stop1();
    motor_stop2();
    delay(600);

    float y = YaccValue();
    motor_CW1();
    while (y > Yval1){
      y = YaccValue();
      delay(7);
    }
    
    motor_stop1();
    delay(600);
    motor_CCW1();
    motor_CCW2();
    delay(3000);
    motor_stop1();
    motor_stop2();
    
    path1();
  }

 
}


void done(){

  int SB1 = digitalRead (IRB1);
  int SB2 = digitalRead (IRB2);
  Serial.println("in done");
  motor_CCW1();
  motor_CCW2();
  while(SB1 == 0 || SB2 == 0){
   SB1 = digitalRead (IRB1);
   SB2 = digitalRead (IRB2);
   delay(150);
  }  
  motor_stop1();
  motor_stop2();
}



//////////////////////////////////////////////////////////////
void motorBrush_OFF(){
  digitalWrite(brushPin1, LOW);
  digitalWrite(brushPin2, LOW);
  analogWrite(brushPWM, 0);
}
void motorBrush_ON(){
  digitalWrite(brushPin1, HIGH);
  digitalWrite(brushPin2, LOW);
  analogWrite(brushPWM, 250);
}

void motor_stop1(){
  digitalWrite(Pin_D1_L1, LOW);
  digitalWrite(Pin_D2_L1, LOW);
  analogWrite(Pin_E_L1, 0);
}

void motor_stop2(){
  digitalWrite(Pin_D1_L2, LOW);
  digitalWrite(Pin_D2_L2, LOW);
  analogWrite(Pin_E_L2, 0);
}

void motor_CW1(){
  analogWrite(Pin_E_L1, 200);
  digitalWrite(Pin_D1_L1, HIGH);
  digitalWrite(Pin_D2_L1, LOW);  
}
void motor_CW2(){
  analogWrite(Pin_E_L2, 200);
  digitalWrite(Pin_D1_L2, HIGH);
  digitalWrite(Pin_D2_L2, LOW);  
}
void motor_CCW1(){
  analogWrite(Pin_E_L1, 200);
  digitalWrite(Pin_D1_L1, LOW);
  digitalWrite(Pin_D2_L1, HIGH);  
}
void motor_CCW2(){
  analogWrite(Pin_E_L2, 200);
  digitalWrite(Pin_D1_L2, LOW);
  digitalWrite(Pin_D2_L2, HIGH);  
}

float XaccValue(){
  mpu.update();  
  return mpu.getAngleX();  
}
float YaccValue(){
  mpu.update();  
  return mpu.getAngleY();  
}
float ZaccValue(){
  mpu.update();  
  return mpu.getAngleZ();  
}

void motorPump_OFF(){
  digitalWrite(pumpPin1, LOW);
  digitalWrite(pumpPin2, LOW);
  analogWrite(pumpPWM, 0);
  statePump = 0;
}
void motorPump_ON(){
  digitalWrite(pumpPin1, HIGH);
  digitalWrite(pumpPin2, LOW);
  analogWrite(pumpPWM, 250);
  statePump = 1;
}

void pumpWater(){

  motorPump_ON();

  while(statePump == 1){
    if(millis() - prevTime >= delayON){
       Serial.println("motor will turn off");
       motorPump_OFF();
       prevTime = millis();
    }
   }
 while(statePump == 0) {
    if(millis() - prevTime >= delayOFF){
      Serial.println("motor will turn on");
      prevTime = millis();
      
      
      if(pump == 1)
      pumpWater();
    } 
  }
  Serial.println(millis());
}

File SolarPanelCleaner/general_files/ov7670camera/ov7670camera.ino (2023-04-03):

#include <stdint.h>

#include <avr/io.h>

#include <util/twi.h>

#include <util/delay.h>

#include <avr/pgmspace.h>


#define F_CPU 16000000UL

#define vga   0

#define qvga  1

#define qqvga   2

#define yuv422  0

#define rgb565  1

#define bayerRGB  2

#define camAddr_WR  0x42

#define camAddr_RD  0x43


/* Registers */

#define REG_GAIN    0x00  /* Gain lower 8 bits (rest in vref) */

#define REG_BLUE    0x01  /* blue gain */

#define REG_RED       0x02  /* red gain */

#define REG_VREF    0x03  /* Pieces of GAIN, VSTART, VSTOP */

#define REG_COM1    0x04  /* Control 1 */

#define COM1_CCIR656  0x40    /* CCIR656 enable */


#define REG_BAVE    0x05  /* U/B Average level */

#define REG_GbAVE   0x06  /* Y/Gb Average level */

#define REG_AECHH   0x07  /* AEC MS 5 bits */

#define REG_RAVE    0x08  /* V/R Average level */

#define REG_COM2    0x09  /* Control 2 */

#define COM2_SSLEEP         0x10  /* Soft sleep mode */

#define REG_PID           0x0a  /* Product ID MSB */

#define REG_VER           0x0b  /* Product ID LSB */

#define REG_COM3    0x0c  /* Control 3 */

#define COM3_SWAP         0x40  /* Byte swap */

#define COM3_SCALEEN          0x08  /* Enable scaling */

#define COM3_DCWEN          0x04  /* Enable downsamp/crop/window */

#define REG_COM4    0x0d  /* Control 4 */

#define REG_COM5    0x0e  /* All "reserved" */

#define REG_COM6    0x0f  /* Control 6 */

#define REG_AECH    0x10  /* More bits of AEC value */

#define REG_CLKRC   0x11  /* Clocl control */

#define CLK_EXT           0x40  /* Use external clock directly */

#define CLK_SCALE   0x3f  /* Mask for internal clock scale */

#define REG_COM7    0x12  /* Control 7 */ //REG mean address.

#define COM7_RESET          0x80  /* Register reset */

#define COM7_FMT_MASK         0x38

#define COM7_FMT_VGA          0x00

#define COM7_FMT_CIF          0x20  /* CIF format */

#define COM7_FMT_QVGA         0x10  /* QVGA format */

#define COM7_FMT_QCIF         0x08  /* QCIF format */

#define COM7_RGB          0x04  /* bits 0 and 2 - RGB format */

#define COM7_YUV          0x00  /* YUV */

#define COM7_BAYER          0x01  /* Bayer format */

#define COM7_PBAYER         0x05  /* "Processed bayer" */

#define REG_COM8    0x13  /* Control 8 */

#define COM8_FASTAEC          0x80  /* Enable fast AGC/AEC */

#define COM8_AECSTEP          0x40  /* Unlimited AEC step size */

#define COM8_BFILT    0x20  /* Band filter enable */

#define COM8_AGC    0x04  /* Auto gain enable */

#define COM8_AWB    0x02  /* White balance enable */

#define COM8_AEC    0x01  /* Auto exposure enable */

#define REG_COM9    0x14  /* Control 9- gain ceiling */

#define REG_COM10   0x15  /* Control 10 */

#define COM10_HSYNC         0x40  /* HSYNC instead of HREF */

#define COM10_PCLK_HB         0x20  /* Suppress PCLK on horiz blank */

#define COM10_HREF_REV          0x08  /* Reverse HREF */

#define COM10_VS_LEAD         0x04  /* VSYNC on clock leading edge */

#define COM10_VS_NEG          0x02  /* VSYNC negative */

#define COM10_HS_NEG          0x01  /* HSYNC negative */

#define REG_HSTART    0x17  /* Horiz start high bits */

#define REG_HSTOP   0x18  /* Horiz stop high bits */

#define REG_VSTART    0x19  /* Vert start high bits */

#define REG_VSTOP   0x1a  /* Vert stop high bits */

#define REG_PSHFT   0x1b  /* Pixel delay after HREF */

#define REG_MIDH    0x1c  /* Manuf. ID high */

#define REG_MIDL    0x1d  /* Manuf. ID low */

#define REG_MVFP    0x1e  /* Mirror / vflip */

#define MVFP_MIRROR         0x20  /* Mirror image */

#define MVFP_FLIP   0x10  /* Vertical flip */


#define REG_AEW           0x24  /* AGC upper limit */

#define REG_AEB           0x25    /* AGC lower limit */

#define REG_VPT           0x26  /* AGC/AEC fast mode op region */

#define REG_HSYST   0x30  /* HSYNC rising edge delay */

#define REG_HSYEN   0x31  /* HSYNC falling edge delay */

#define REG_HREF    0x32  /* HREF pieces */

#define REG_TSLB    0x3a  /* lots of stuff */

#define TSLB_YLAST    0x04  /* UYVY or VYUY - see com13 */

#define REG_COM11   0x3b  /* Control 11 */

#define COM11_NIGHT         0x80  /* NIght mode enable */

#define COM11_NMFR          0x60  /* Two bit NM frame rate */

#define COM11_HZAUTO          0x10  /* Auto detect 50/60 Hz */

#define COM11_50HZ          0x08  /* Manual 50Hz select */

#define COM11_EXP   0x02

#define REG_COM12   0x3c  /* Control 12 */

#define COM12_HREF          0x80  /* HREF always */

#define REG_COM13   0x3d  /* Control 13 */

#define COM13_GAMMA         0x80  /* Gamma enable */

#define COM13_UVSAT         0x40  /* UV saturation auto adjustment */

#define COM13_UVSWAP          0x01  /* V before U - w/TSLB */

#define REG_COM14   0x3e  /* Control 14 */

#define COM14_DCWEN         0x10  /* DCW/PCLK-scale enable */

#define REG_EDGE    0x3f  /* Edge enhancement factor */

#define REG_COM15   0x40  /* Control 15 */

#define COM15_R10F0         0x00  /* Data range 10 to F0 */

#define COM15_R01FE         0x80  /*      01 to FE */

#define COM15_R00FF         0xc0  /*      00 to FF */

#define COM15_RGB565          0x10  /* RGB565 output */

#define COM15_RGB555          0x30  /* RGB555 output */

#define REG_COM16   0x41  /* Control 16 */

#define COM16_AWBGAIN         0x08  /* AWB gain enable */

#define REG_COM17   0x42  /* Control 17 */

#define COM17_AECWIN          0xc0  /* AEC window - must match COM4 */

#define COM17_CBAR          0x08  /* DSP Color bar */

/*

* This matrix defines how the colors are generated, must be

* tweaked to adjust hue and saturation.

*

* Order: v-red, v-green, v-blue, u-red, u-green, u-blue

* They are nine-bit signed quantities, with the sign bit

* stored in0x58.Sign for v-red is bit 0, and up from there.

*/

#define REG_CMATRIX_BASE  0x4f

#define CMATRIX_LEN           6

#define REG_CMATRIX_SIGN  0x58

#define REG_BRIGHT    0x55  /* Brightness */

#define REG_CONTRAS         0x56  /* Contrast control */

#define REG_GFIX    0x69  /* Fix gain control */

#define REG_REG76   0x76  /* OV's name */

#define R76_BLKPCOR         0x80  /* Black pixel correction enable */

#define R76_WHTPCOR         0x40  /* White pixel correction enable */

#define REG_RGB444          0x8c  /* RGB 444 control */

#define R444_ENABLE         0x02  /* Turn on RGB444, overrides 5x5 */

#define R444_RGBX   0x01  /* Empty nibble at end */

#define REG_HAECC1    0x9f  /* Hist AEC/AGC control 1 */

#define REG_HAECC2    0xa0  /* Hist AEC/AGC control 2 */

#define REG_BD50MAX         0xa5  /* 50hz banding step limit */

#define REG_HAECC3    0xa6  /* Hist AEC/AGC control 3 */

#define REG_HAECC4    0xa7  /* Hist AEC/AGC control 4 */

#define REG_HAECC5    0xa8  /* Hist AEC/AGC control 5 */

#define REG_HAECC6    0xa9  /* Hist AEC/AGC control 6 */

#define REG_HAECC7    0xaa  /* Hist AEC/AGC control 7 */

#define REG_BD60MAX         0xab  /* 60hz banding step limit */

#define REG_GAIN    0x00  /* Gain lower 8 bits (rest in vref) */
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
